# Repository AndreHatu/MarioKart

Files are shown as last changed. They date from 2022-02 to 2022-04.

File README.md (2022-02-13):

# Mario Kart with RC cars and ESP32s
This project aims at developing a real-life Mario Kart with RC cars and ESP32s.
The boards used utilize a single-core MCU (ESP-MINI-1 and ESP-SOLO-1). 
Schematics and wiring will be posted in the near future.

ECE477 Senior Design at Purdue University.

## How it works
We control RC cars with electronics replaced by our own ESP32. All communications are made using ESP-NOW, which is a Wi-Fi like wireless communication protocol. It enables low latency and long distance transmission of packets, with the only restriction they must be less than 250 bytes long.
Then, we place checkpoint towers and power-up blocks along the desired track and when cars run over them, a NFC tag is read and its information is sent to a central tower, which either updates records of checkpoints or determines what modifier to give the cars. Modifiers are randomly chosen using ESP's ```esp_random()``` function. Checkpoints are stored in two-dimensional arrays initialized upon race creation.

## Cloning
When cloning this repo, make sure to use ```git clone --recursive git@github.com:AndreHatu/MarioKart.git``` or run ```git submodule update --init --recursive``` after doing a standard clone. 
This ensures all dependencies are downloaded.

## Config, Build and Flash
To build, you will need to have installed Espressif's idf from their website.
Then run the following commands from a terminal.

```
idf.py set-target esp32
idf.py menuconfig
```
Inside the menuconfig, you might need to set the ```Components->freeRTOS->Run only on first core``` option in case your ESP32 only has one core (like the ones we are using for the project)
Then you can build and flash with
```
idf.py build
idf.py -p (PORT) flash
```

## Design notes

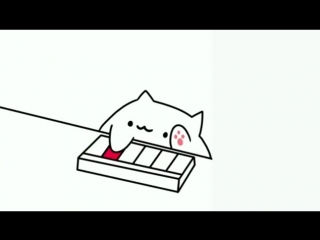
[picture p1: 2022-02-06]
spi_practice/main/image.jpg

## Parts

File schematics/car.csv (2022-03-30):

Source: | C:\Users\andre\prog\MarioKart\schematics\car.kicad_sch
Date: | 3/11/2022 11:44:14 AM
Tool: | Eeschema (6.0.2)
Generator: | C:\Program Files\KiCad\6.0\bin\scripting\plugins/bom_csv_grouped_by_value_with_fp.py
Component Count: | 44
Ref | Qnty | Value | Cmp name | Footprint | Description | Vendor
C1, | 1 | 22uF | C | Capacitor_SMD:C_0805_2012Metric | Unpolarized capacitor
C2, C4, C5, C6, | 4 | 100nF | C | Capacitor_SMD:C_0805_2012Metric | Unpolarized capacitor
C3, C7, | 2 | 100uF | C | Capacitor_THT:CP_Radial_D8.0mm_P5.00mm | Unpolarized capacitor
D1, D2, D3, D4, D5, D6, D7, D8, | 8 | IN4148 | DIODE | Diode_SMD:D_SOD-123F | Diode symbol for simulation only. Pin order incompatible with official kicad footprints
D9, | 1 | LED | LED | SamacSys_Parts:APHCM2012QBCDF01 | Light emitting diode
H1, H2, H3, H4, | 4 | MountingHole | MountingHole | MountingHole:MountingHole_2.5mm_Pad | Mounting Hole without connection
IC1, | 1 | ESP32-SOLO-1 | ESP32-SOLO-1 | RF_Module:ESP32-SOLO-ONE
J1, | 1 | Conn_01x09_Female | Conn_01x09_Female | Connector_PinHeader_2.54mm:PinHeader_1x09_P2.54mm_Vertical | Generic connector, single row, 01x09, script generated (kicad-library-utils/schlib/autogen/connector/)
J2, | 1 | Conn_01x04_Male | Conn_01x04_Male | Connector_PinHeader_2.54mm:PinHeader_1x04_P2.54mm_Vertical | Generic connector, single row, 01x04, script generated (kicad-library-utils/schlib/autogen/connector/)
J3, | 1 | Conn_01x02_Female | Conn_01x02_Female | Connector_PinHeader_2.54mm:PinHeader_1x02_P2.54mm_Vertical | Generic connector, single row, 01x02, script generated (kicad-library-utils/schlib/autogen/connector/)
J4, | 1 | Conn_01x06_Female | Conn_01x06_Female | Connector_PinHeader_2.54mm:PinHeader_1x06_P2.54mm_Vertical | Generic connector, single row, 01x06, script generated (kicad-library-utils/schlib/autogen/connector/)
J5, J6, | 2 | Conn_01x05_Female | Conn_01x05_Female | Connector_PinHeader_2.54mm:PinHeader_1x05_P2.54mm_Vertical | Generic connector, single row, 01x05, script generated (kicad-library-utils/schlib/autogen/connector/)
Q1, Q2, | 2 | SS8050-G | SS8050-G | SamacSys_Parts:SOT95P240X115-3N | Bipolar Transistors - BJT NPN TRANSISTOR 1.5A 40V
R1, R2, R3, R4, R5, R6, | 6 | 20 | R | Resistor_SMD:R_0805_2012Metric | Resistor
R7, R8, R9, R10, R11, R12, | 6 | 10k | R | Resistor_SMD:R_0805_2012Metric | Resistor
SW1, SW2, | 2 | SW_Push | SW_Push | Button_Switch_SMD:SW_SPST_CK_KXT3 | Push button switch, generic, two pins
U1, | 1 | L298HN | L298HN | Package_TO_SOT_THT:TO-220-15_P2.54x2.54mm_StaggerOdd_Lead4.58mm_Vertical | Dual full bridge motor driver, up to 46V, 4A, Multiwatt-15

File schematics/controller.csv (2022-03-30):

Source: | C:\Users\andre\prog\MarioKart\schematics\controller.kicad_sch
Date: | 3/11/2022 11:44:30 AM
Tool: | Eeschema (6.0.2)
Generator: | C:\Program Files\KiCad\6.0\bin\scripting\plugins/bom_csv_grouped_by_value.py
Component Count: | 33
Individual Components:
Item | Qty | Reference(s) | Value | LibPart | Footprint | Datasheet | Description | Height | Manufacturer_Name | Manufacturer_Part_Number | Mouser Part Number | Mouser Price/Stock
 |  | C1 | 0.1uF | Device:C | Capacitor_SMD:C_0805_2012Metric | ~
 |  | C2 | 0.1uF | Device:C | Capacitor_SMD:C_0805_2012Metric | ~
 |  | C3 | 100nF | Device:C | Capacitor_SMD:C_0805_2012Metric | ~
 |  | C4 | 22uF | Device:C | Capacitor_SMD:C_0805_2012Metric | ~
 |  | C5 | 100nF | Device:C | Capacitor_SMD:C_0805_2012Metric | ~
 |  | C6 | 10uF | Device:C | Capacitor_SMD:C_0805_2012Metric | ~
 |  | C7 | 10uF | Device:C | Capacitor_SMD:C_0805_2012Metric | ~
 |  | D1 | LED | Device:LED | Mouser:APHCM2012QBCDF01 | ~
 |  | IC1 | AZ1117CD-3.3TRG1 | Mouser:AZ1117CD-3.3TRG1 | Mouser:AZ1117CD33TRG1 | https://www.diodes.com/assets/Datasheets/AZ1117C.pdf | LDO Regulator Pos 3.3V 0.8A 3-Pin(2+Tab) TO-252 T/R | 2.38 | Diodes Inc. | AZ1117CD-3.3TRG1 | 621-AZ1117CD-3.3TRG1 | https://www.mouser.co.uk/ProductDetail/Diodes-Incorporated/AZ1117CD-33TRG1?qs=FKu9oBikfSnei3n4%2FTBoVg%3D%3D
 |  | IC2 | ESP32-SOLO-1 | ESP-SOLO-1:ESP32-SOLO-1 | RF_Module:ESP32-WROOM-32 | https://www.espressif.com/sites/default/files/documentation/esp32-solo-1_datasheet_en.pdf | WiFi Modules (802.11) SMD Module, ESP32-S0WD, 32Mbits SPI flash, UART mode, |  | Espressif Systems | ESP32-SOLO-1 | 356-ESP32-SOLO-1 | https://www.mouser.co.uk/ProductDetail/Espressif-Systems/ESP32-SOLO-1?qs=w%2Fv1CP2dgqpIFRWX9FvikA%3D%3D
 |  | J1 | Conn_01x05 | Connector_Generic:Conn_01x05 | Connector_PinSocket_2.54mm:PinSocket_1x05_P2.54mm_Vertical | ~
 |  | J2 | Conn_01x05 | Connector_Generic:Conn_01x05 | Connector_PinSocket_2.54mm:PinSocket_1x05_P2.54mm_Vertical | ~
 |  | J3 | Conn_01x06 | Connector_Generic:Conn_01x06 | Connector_PinSocket_2.54mm:PinSocket_1x06_P2.54mm_Vertical | ~
 |  | Q1 | SS8050-G | Mouser:SS8050-G | Mouser:SOT95P240X115-3N | https://datasheet.datasheetarchive.com/originals/distributors/DKDS-12/229454.pdf | Bipolar Transistors - BJT NPN TRANSISTOR 1.5A 40V | 1.15 | Comchip Technology | SS8050-G | 750-SS8050-G | https://www.mouser.co.uk/ProductDetail/Comchip-Technology/SS8050-G?qs=LLUE9lz1YbcHg%252BWLMAtcrQ%3D%3D
 |  | Q2 | SS8050-G | Mouser:SS8050-G | Mouser:SOT95P240X115-3N | https://datasheet.datasheetarchive.com/originals/distributors/DKDS-12/229454.pdf | Bipolar Transistors - BJT NPN TRANSISTOR 1.5A 40V | 1.15 | Comchip Technology | SS8050-G | 750-SS8050-G | https://www.mouser.co.uk/ProductDetail/Comchip-Technology/SS8050-G?qs=LLUE9lz1YbcHg%252BWLMAtcrQ%3D%3D
 |  | R1 | 10k | Device:R | Resistor_SMD:R_0805_2012Metric | ~
 |  | R2 | 10k | Device:R | Resistor_SMD:R_0805_2012Metric | ~
 |  | R3 | 10k | Device:R | Resistor_SMD:R_0805_2012Metric | ~
 |  | R4 | 10k | Device:R | Resistor_SMD:R_0805_2012Metric | ~
 |  | R5 | 10k | Device:R | Resistor_SMD:R_0805_2012Metric | ~
 |  | R6 | 10k | Device:R | Resistor_SMD:R_0805_2012Metric | ~
 |  | R7 | 10k | Device:R | Resistor_SMD:R_0805_2012Metric | ~
 |  | R8 | 10k | Device:R | Resistor_SMD:R_0805_2012Metric | ~
 |  | R9 | 0 | Device:R | Resistor_SMD:R_0805_2012Metric | ~
 |  | R10 | 10k | Device:R | Resistor_SMD:R_0805_2012Metric | ~
 |  | R11 | 10k | Device:R | Resistor_SMD:R_0805_2012Metric | ~
 |  | SW1 | SW_Push | Switch:SW_Push | Button_Switch_SMD:SW_SPST_CK_KXT3 | ~
 |  | SW2 | SW_Push | Switch:SW_Push | Button_Switch_SMD:SW_SPST_CK_KXT3 | ~
 |  | SW3 | SW_Push_Dual | Switch:SW_Push_Dual | Button_Switch_THT:SW_TH_Tactile_Omron_B3F-10xx | ~
 |  | SW4 | SW_Push_Dual | Switch:SW_Push_Dual | Button_Switch_THT:SW_TH_Tactile_Omron_B3F-10xx | ~
 |  | SW5 | SW_Push_Dual | Switch:SW_Push_Dual | Button_Switch_THT:SW_TH_Tactile_Omron_B3F-10xx | ~
 |  | SW6 | SW_Push_Dual | Switch:SW_Push_Dual | Button_Switch_THT:SW_TH_Tactile_Omron_B3F-10xx | ~
 |  | SW7 | SW_Push_Dual | Switch:SW_Push_Dual | Button_Switch_THT:SW_TH_Tactile_Omron_B3F-10xx | ~
Collated Components:
Item | Qty | Reference(s) | Value | LibPart | Footprint | Datasheet | Description | Height | Manufacturer_Name | Manufacturer_Part_Number | Mouser Part Number | Mouser Price/Stock
1 | 2 | C1, C2 | 0.1uF | Device:C | Capacitor_SMD:C_0805_2012Metric | ~
2 | 2 | C3, C5 | 100nF | Device:C | Capacitor_SMD:C_0805_2012Metric | ~
3 | 1 | C4 | 22uF | Device:C | Capacitor_SMD:C_0805_2012Metric | ~
4 | 2 | C6, C7 | 10uF | Device:C | Capacitor_SMD:C_0805_2012Metric | ~
5 | 1 | D1 | LED | Device:LED | Mouser:APHCM2012QBCDF01 | ~
6 | 1 | IC1 | AZ1117CD-3.3TRG1 | Mouser:AZ1117CD-3.3TRG1 | Mouser:AZ1117CD33TRG1 | https://www.diodes.com/assets/Datasheets/AZ1117C.pdf | LDO Regulator Pos 3.3V 0.8A 3-Pin(2+Tab) TO-252 T/R | 2.38 | Diodes Inc. | AZ1117CD-3.3TRG1 | 621-AZ1117CD-3.3TRG1 | https://www.mouser.co.uk/ProductDetail/Diodes-Incorporated/AZ1117CD-33TRG1?qs=FKu9oBikfSnei3n4%2FTBoVg%3D%3D
7 | 1 | IC2 | ESP32-SOLO-1 | ESP-SOLO-1:ESP32-SOLO-1 | RF_Module:ESP32-WROOM-32 | https://www.espressif.com/sites/default/files/documentation/esp32-solo-1_datasheet_en.pdf | WiFi Modules (802.11) SMD Module, ESP32-S0WD, 32Mbits SPI flash, UART mode, |  | Espressif Systems | ESP32-SOLO-1 | 356-ESP32-SOLO-1 | https://www.mouser.co.uk/ProductDetail/Espressif-Systems/ESP32-SOLO-1?qs=w%2Fv1CP2dgqpIFRWX9FvikA%3D%3D
8 | 2 | J1, J2 | Conn_01x05 | Connector_Generic:Conn_01x05 | Connector_PinSocket_2.54mm:PinSocket_1x05_P2.54mm_Vertical | ~
9 | 1 | J3 | Conn_01x06 | Connector_Generic:Conn_01x06 | Connector_PinSocket_2.54mm:PinSocket_1x06_P2.54mm_Vertical | ~
10 | 2 | Q1, Q2 | SS8050-G | Mouser:SS8050-G | Mouser:SOT95P240X115-3N | https://datasheet.datasheetarchive.com/originals/distributors/DKDS-12/229454.pdf | Bipolar Transistors - BJT NPN TRANSISTOR 1.5A 40V | 1.15 | Comchip Technology | SS8050-G | 750-SS8050-G | https://www.mouser.co.uk/ProductDetail/Comchip-Technology/SS8050-G?qs=LLUE9lz1YbcHg%252BWLMAtcrQ%3D%3D
11 | 10 | R1, R2, R3, R4, R5, R6, R7, R8, R10, R11 | 10k | Device:R | Resistor_SMD:R_0805_2012Metric | ~
12 | 1 | R9 | 0 | Device:R | Resistor_SMD:R_0805_2012Metric | ~
13 | 2 | SW1, SW2 | SW_Push | Switch:SW_Push | Button_Switch_SMD:SW_SPST_CK_KXT3 | ~
14 | 5 | SW3, SW4, SW5, SW6, SW7 | SW_Push_Dual | Switch:SW_Push_Dual | Button_Switch_THT:SW_TH_Tactile_Omron_B3F-10xx | ~

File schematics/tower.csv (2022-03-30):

Source: | C:\Users\andre\prog\MarioKart\schematics\tower.kicad_sch
Date: | 3/11/2022 11:44:42 AM
Tool: | Eeschema (6.0.2)
Generator: | C:\Program Files\KiCad\6.0\bin\scripting\plugins/bom_csv_grouped_by_value.py
Component Count: | 27
Individual Components:
Item | Qty | Reference(s) | Value | LibPart | Footprint | Datasheet | Description | Height | Manufacturer_Name | Manufacturer_Part_Number | Mouser Part Number | Mouser Price/Stock
 |  | C1 | 0.1uF | Device:C | Capacitor_SMD:C_0805_2012Metric | ~
 |  | C2 | 0.1uF | Device:C | Capacitor_SMD:C_0805_2012Metric | ~
 |  | C3 | 100nF | Device:C | Capacitor_SMD:C_0805_2012Metric | ~
 |  | C4 | 22uF | Device:C | Capacitor_SMD:C_0805_2012Metric | ~
 |  | C5 | 100nF | Device:C | Capacitor_SMD:C_0805_2012Metric | ~
 |  | C6 | 100nF | Device:C | Capacitor_SMD:C_0805_2012Metric | ~
 |  | C7 | 100nF | Device:C | Capacitor_SMD:C_0805_2012Metric | ~
 |  | D1 | BAT760-7 | Mouser:BAT760-7 | Mouser:SOD2513X120N | https://www.diodes.com/assets/Datasheets/ds30498.pdf | Diode Schottky 30V 1A 2Pin SOD323 Diodes Inc BAT760-7, SMT Schottky Diode, 30V 1A, 2-Pin SOD-323 | 1.2 | Diodes Inc. | BAT760-7 | 621-BAT760-7 | https://www.mouser.co.uk/ProductDetail/Diodes-Incorporated/BAT760-7?qs=JV7lzlMm3yKDDyO09xoRbQ%3D%3D
 |  | D2 | LED | Device:LED | Mouser:APHCM2012QBCDF01 | ~
 |  | IC1 | ESP32-SOLO-1 | tower-rescue:ESP32-SOLO-1-ESP-SOLO-1-controller-rescue | RF_Module:ESP32-WROOM-32 | https://www.espressif.com/sites/default/files/documentation/esp32-solo-1_datasheet_en.pdf | WiFi Modules (802.11) SMD Module, ESP32-S0WD, 32Mbits SPI flash, UART mode, |  | Espressif Systems | ESP32-SOLO-1 | 356-ESP32-SOLO-1 | https://www.mouser.co.uk/ProductDetail/Espressif-Systems/ESP32-SOLO-1?qs=w%2Fv1CP2dgqpIFRWX9FvikA%3D%3D
 |  | J1 | USB_B_Micro | Connector:USB_B_Micro | Connector_USB:USB_Micro-B_Molex-105017-0001 | ~
 |  | J2 | Conn_01x06 | Connector_Generic:Conn_01x06 | Connector_PinSocket_2.54mm:PinSocket_1x06_P2.54mm_Vertical | ~
 |  | J3 | Conn_01x05 | Connector_Generic:Conn_01x05 | Connector_PinSocket_2.54mm:PinSocket_1x05_P2.54mm_Vertical | ~
 |  | J4 | SD_Card | Connector:SD_Card | Connector_Card:SD_Kyocera_145638109211859+ | http://portal.fciconnect.com/Comergent//fci/drawing/10067847.pdf
 |  | J5 | Conn_02x10_Odd_Even | Connector_Generic:Conn_02x10_Odd_Even | Connector_PinSocket_2.54mm:PinSocket_2x10_P2.54mm_Vertical | ~
 |  | Q1 | SS8050-G | Mouser:SS8050-G | Mouser:SOT95P240X115-3N | https://datasheet.datasheetarchive.com/originals/distributors/DKDS-12/229454.pdf | Bipolar Transistors - BJT NPN TRANSISTOR 1.5A 40V | 1.15 | Comchip Technology | SS8050-G | 750-SS8050-G | https://www.mouser.co.uk/ProductDetail/Comchip-Technology/SS8050-G?qs=LLUE9lz1YbcHg%252BWLMAtcrQ%3D%3D
 |  | Q2 | SS8050-G | Mouser:SS8050-G | Mouser:SOT95P240X115-3N | https://datasheet.datasheetarchive.com/originals/distributors/DKDS-12/229454.pdf | Bipolar Transistors - BJT NPN TRANSISTOR 1.5A 40V | 1.15 | Comchip Technology | SS8050-G | 750-SS8050-G | https://www.mouser.co.uk/ProductDetail/Comchip-Technology/SS8050-G?qs=LLUE9lz1YbcHg%252BWLMAtcrQ%3D%3D
 |  | R1 | 10k | Device:R | Resistor_SMD:R_0805_2012Metric | ~
 |  | R2 | 10k | Device:R | Resistor_SMD:R_0805_2012Metric | ~
 |  | R3 | 10k | Device:R | Resistor_SMD:R_0805_2012Metric | ~
 |  | R4 | 10k | Device:R | Resistor_SMD:R_0805_2012Metric | ~
 |  | R5 | 10k | Device:R | Resistor_SMD:R_0805_2012Metric | ~
 |  | R6 | 0 | Device:R | Resistor_SMD:R_0805_2012Metric | ~
 |  | R7 | 0 | Device:R | Resistor_SMD:R_0805_2012Metric | ~
 |  | R8 | 10k | Device:R | Resistor_SMD:R_0805_2012Metric | ~
 |  | SW1 | SW_Push | Switch:SW_Push | Button_Switch_SMD:SW_SPST_CK_KXT3 | ~
 |  | SW2 | SW_Push | Switch:SW_Push | Button_Switch_SMD:SW_SPST_CK_KXT3 | ~
Collated Components:
Item | Qty | Reference(s) | Value | LibPart | Footprint | Datasheet | Description | Height | Manufacturer_Name | Manufacturer_Part_Number | Mouser Part Number | Mouser Price/Stock
1 | 2 | C1, C2 | 0.1uF | Device:C | Capacitor_SMD:C_0805_2012Metric | ~
2 | 4 | C3, C5, C6, C7 | 100nF | Device:C | Capacitor_SMD:C_0805_2012Metric | ~
3 | 1 | C4 | 22uF | Device:C | Capacitor_SMD:C_0805_2012Metric | ~
4 | 1 | D1 | BAT760-7 | Mouser:BAT760-7 | Mouser:SOD2513X120N | https://www.diodes.com/assets/Datasheets/ds30498.pdf | Diode Schottky 30V 1A 2Pin SOD323 Diodes Inc BAT760-7, SMT Schottky Diode, 30V 1A, 2-Pin SOD-323 | 1.2 | Diodes Inc. | BAT760-7 | 621-BAT760-7 | https://www.mouser.co.uk/ProductDetail/Diodes-Incorporated/BAT760-7?qs=JV7lzlMm3yKDDyO09xoRbQ%3D%3D
5 | 1 | D2 | LED | Device:LED | Mouser:APHCM2012QBCDF01 | ~
6 | 1 | IC1 | ESP32-SOLO-1 | tower-rescue:ESP32-SOLO-1-ESP-SOLO-1-controller-rescue | RF_Module:ESP32-WROOM-32 | https://www.espressif.com/sites/default/files/documentation/esp32-solo-1_datasheet_en.pdf | WiFi Modules (802.11) SMD Module, ESP32-S0WD, 32Mbits SPI flash, UART mode, |  | Espressif Systems | ESP32-SOLO-1 | 356-ESP32-SOLO-1 | https://www.mouser.co.uk/ProductDetail/Espressif-Systems/ESP32-SOLO-1?qs=w%2Fv1CP2dgqpIFRWX9FvikA%3D%3D
7 | 1 | J1 | USB_B_Micro | Connector:USB_B_Micro | Connector_USB:USB_Micro-B_Molex-105017-0001 | ~
8 | 1 | J2 | Conn_01x06 | Connector_Generic:Conn_01x06 | Connector_PinSocket_2.54mm:PinSocket_1x06_P2.54mm_Vertical | ~
9 | 1 | J3 | Conn_01x05 | Connector_Generic:Conn_01x05 | Connector_PinSocket_2.54mm:PinSocket_1x05_P2.54mm_Vertical | ~
10 | 1 | J4 | SD_Card | Connector:SD_Card | Connector_Card:SD_Kyocera_145638109211859+ | http://portal.fciconnect.com/Comergent//fci/drawing/10067847.pdf
11 | 1 | J5 | Conn_02x10_Odd_Even | Connector_Generic:Conn_02x10_Odd_Even | Connector_PinSocket_2.54mm:PinSocket_2x10_P2.54mm_Vertical | ~
12 | 2 | Q1, Q2 | SS8050-G | Mouser:SS8050-G | Mouser:SOT95P240X115-3N | https://datasheet.datasheetarchive.com/originals/distributors/DKDS-12/229454.pdf | Bipolar Transistors - BJT NPN TRANSISTOR 1.5A 40V | 1.15 | Comchip Technology | SS8050-G | 750-SS8050-G | https://www.mouser.co.uk/ProductDetail/Comchip-Technology/SS8050-G?qs=LLUE9lz1YbcHg%252BWLMAtcrQ%3D%3D
13 | 6 | R1, R2, R3, R4, R5, R8 | 10k | Device:R | Resistor_SMD:R_0805_2012Metric | ~
14 | 2 | R6, R7 | 0 | Device:R | Resistor_SMD:R_0805_2012Metric | ~
15 | 2 | SW1, SW2 | SW_Push | Switch:SW_Push | Button_Switch_SMD:SW_SPST_CK_KXT3 | ~

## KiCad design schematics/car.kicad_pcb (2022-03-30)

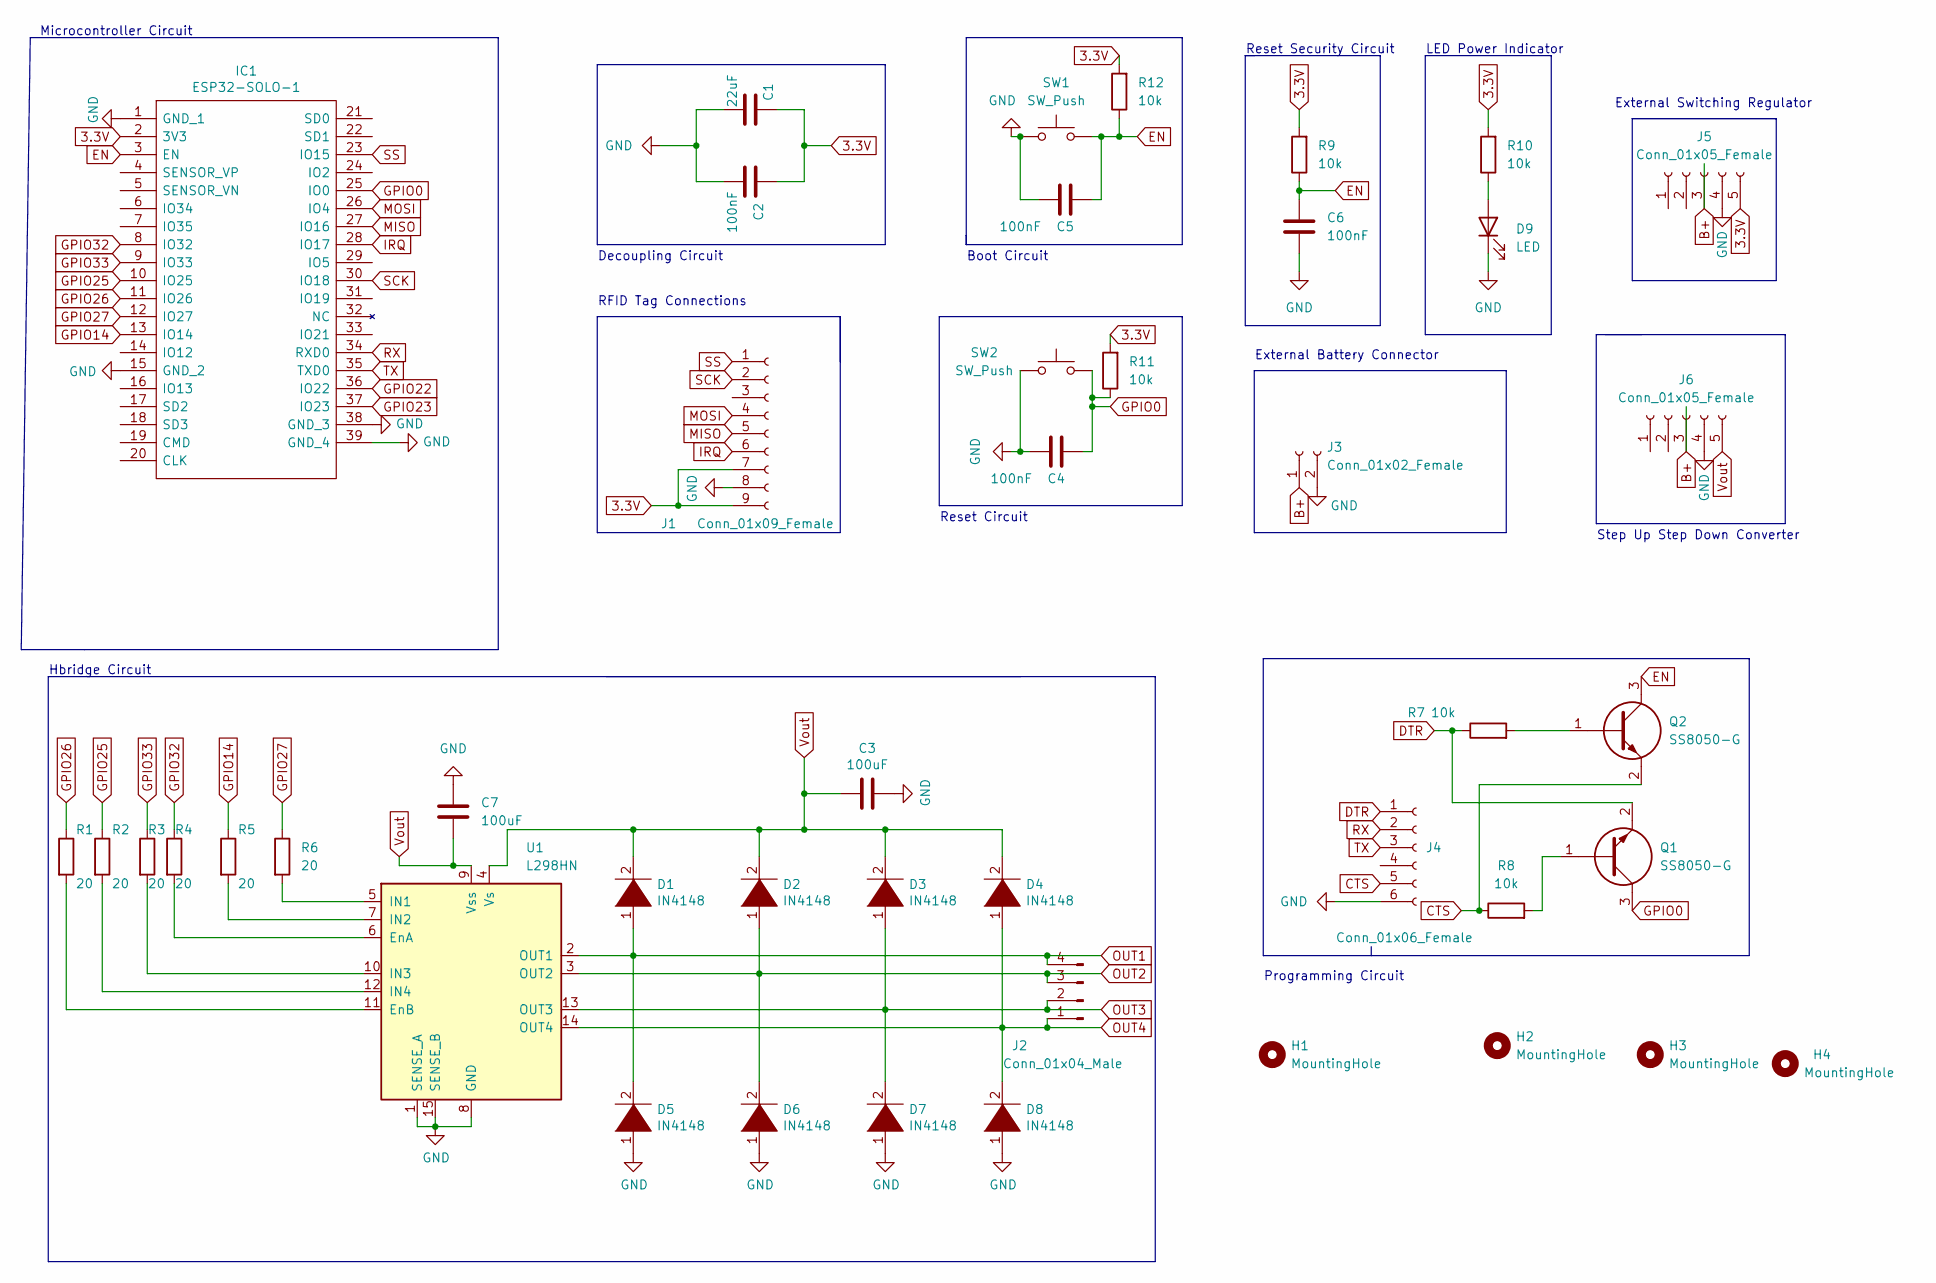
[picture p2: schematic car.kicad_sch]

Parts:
C1: 22uF; C_0805_2012Metric
C2, C4, C5, C6: 100nF; C_0805_2012Metric
C3, C7: 100uF; CP_Radial_D8.0mm_P5.00mm
D1, D2, D3, D4, D5, D6, D7, D8: IN4148; D_SOD-123F
D9: LED; APHCM2012QBCDF01
H1, H2, H3, H4: MountingHole; MountingHole_2.5mm_Pad
IC1: ESP32-SOLO-1; ESP32-SOLO-ONE; Manufacturer_Part_Number ESP32-SOLO-1; Mouser Part Number 356-ESP32-SOLO-1
J1: Conn_01x09_Female; PinHeader_1x09_P2.54mm_Vertical
J2: Conn_01x04_Male; PinHeader_1x04_P2.54mm_Vertical
J3: Conn_01x02_Female; PinHeader_1x02_P2.54mm_Vertical
J4: Conn_01x06_Female; PinHeader_1x06_P2.54mm_Vertical
J5, J6: Conn_01x05_Female; PinHeader_1x05_P2.54mm_Vertical
Q1, Q2: SS8050-G; SOT95P240X115-3N; Mouser Part Number 750-SS8050-G
R1, R2, R3, R4, R5, R6: 20; R_0805_2012Metric
R7, R8, R9, R10, R11, R12: 10k; R_0805_2012Metric
SW1, SW2: SW_Push; SW_SPST_CK_KXT3
U1: L298HN; TO-220-15_P2.54x2.54mm_StaggerOdd_Lead4.58mm_Vertical

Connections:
3.3V: C1.1, C2.1, IC1.2 (3V3), J1.7, J1.9, J5.5, R9.2, R10.2, R11.2, R12.2
B+: J3.1, J5.3, J6.3
CTS: J4.5, Q2.2, R8.1
DTR: J4.1, Q1.2, R7.1
EN: C5.2, C6.1, IC1.3 (EN), Q2.3, R9.1, R12.1, SW1.2
GND: C1.2, C2.2, C3.1, C4.1, C5.1, C6.2, C7.1, D5.1 (K), D6.1 (K), D7.1 (K), D8.1 (K), D9.1 (K), IC1.1 (GND_1), IC1.15 (GND_2), IC1.38 (GND_3), IC1.39 (GND_4), J1.8, J3.2, J4.6, J5.4, J6.4, SW1.1, SW2.1, U1.1 (SENSE_A), U1.8 (GND), U1.15 (SENSE_B)
GPIO0: C4.2, IC1.25 (IO0), Q1.3, R11.1, SW2.2
GPIO14: IC1.13 (IO14), R5.1
GPIO22: IC1.36 (IO22)
GPIO23: IC1.37 (IO23)
GPIO25: IC1.10 (IO25), R2.1
GPIO26: IC1.11 (IO26), R1.1
GPIO27: IC1.12 (IO27), R6.1
GPIO32: IC1.8 (IO32), R4.1
GPIO33: IC1.9 (IO33), R3.1
IRQ: IC1.28 (IO17), J1.6
MISO: IC1.27 (IO16), J1.5
MOSI: IC1.26 (IO4), J1.4
unnamed: D9.2 (A), R10.1
unnamed: Q1.1, R8.2
unnamed: Q2.1, R7.2
unnamed: R1.2, U1.11 (EnB)
unnamed: R2.2, U1.12 (IN4)
unnamed: R3.2, U1.10 (IN3)
unnamed: R4.2, U1.6 (EnA)
unnamed: R5.2, U1.7 (IN2)
unnamed: R6.2, U1.5 (IN1)
OUT1: D1.1 (K), D5.2 (A), J2.4, U1.2 (OUT1)
OUT2: D2.1 (K), D6.2 (A), J2.3, U1.3 (OUT2)
OUT3: D3.1 (K), D7.2 (A), J2.2, U1.13 (OUT3)
OUT4: D4.1 (K), D8.2 (A), J2.1, U1.14 (OUT4)
RX: IC1.34 (RXD0), J4.2
SCK: IC1.30 (IO18), J1.2
SS: IC1.23 (IO15), J1.1
TX: IC1.35 (TXD0), J4.3
Vout: C3.2, C7.2, D1.2 (A), D2.2 (A), D3.2 (A), D4.2 (A), J6.5, U1.4 (Vs), U1.9 (Vss)

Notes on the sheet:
Step Up Step Down Converter
Boot Circuit
Microcontroller Circuit
Programming Circuit
External Switching Regulator
External Battery Connector
Hbridge Circuit
Decoupling Circuit
RFID Tag Connections
Reset Circuit
Reset Security Circuit
LED Power Indicator

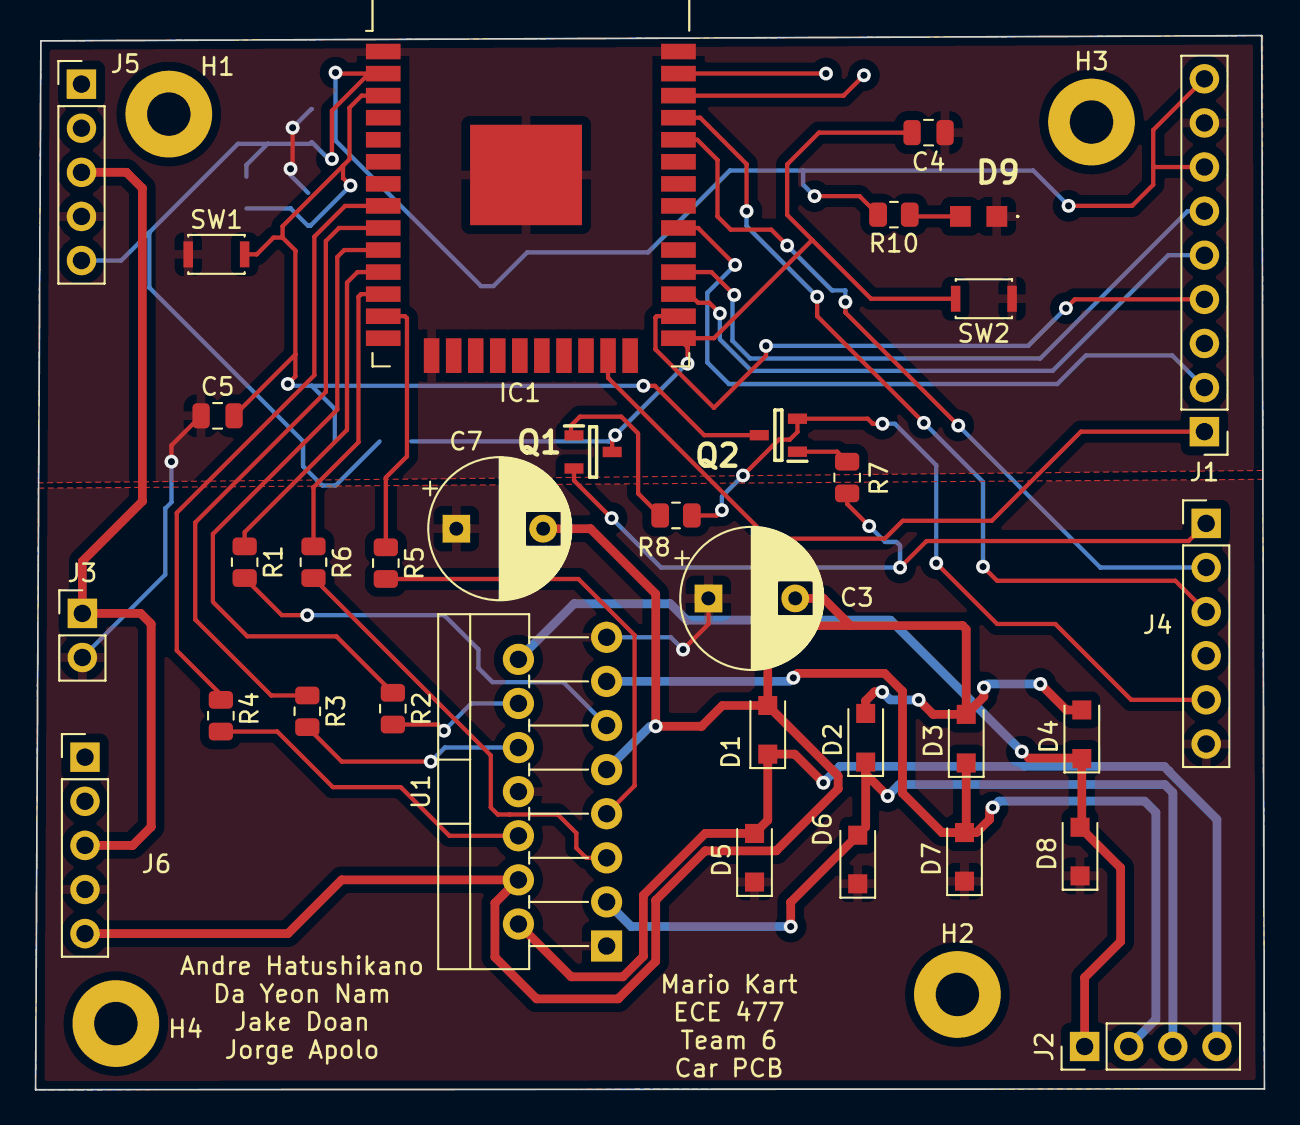
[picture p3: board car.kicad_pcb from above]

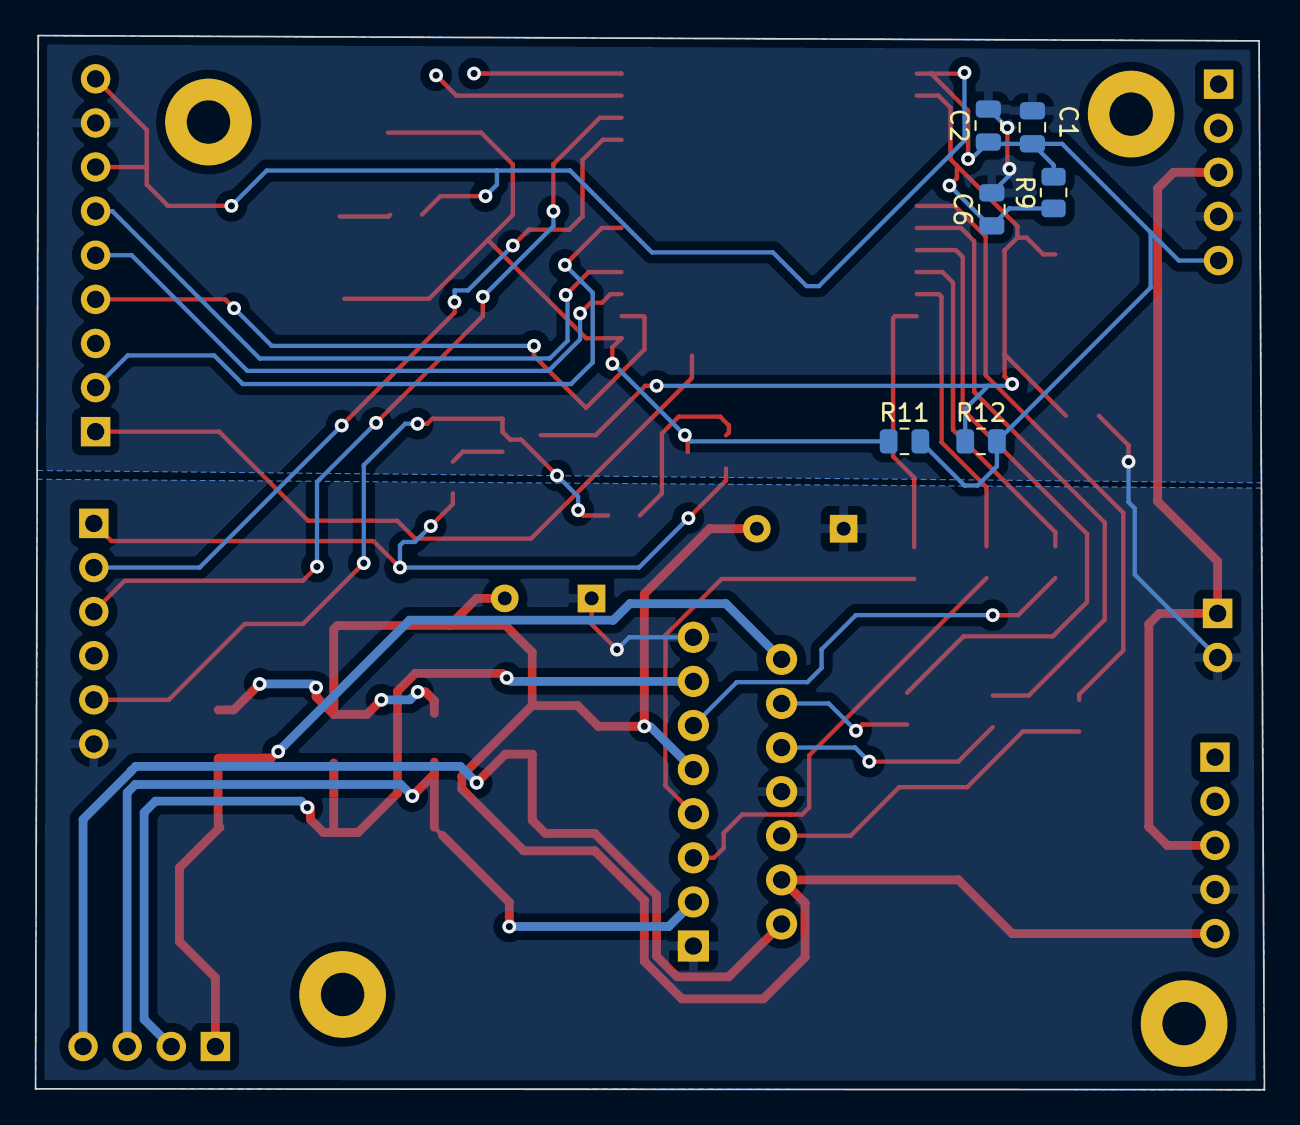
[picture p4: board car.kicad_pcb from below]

Board: 2 copper layers, 70.8 x 60.7 mm, 44 parts (6 on the bottom side), 34 nets.

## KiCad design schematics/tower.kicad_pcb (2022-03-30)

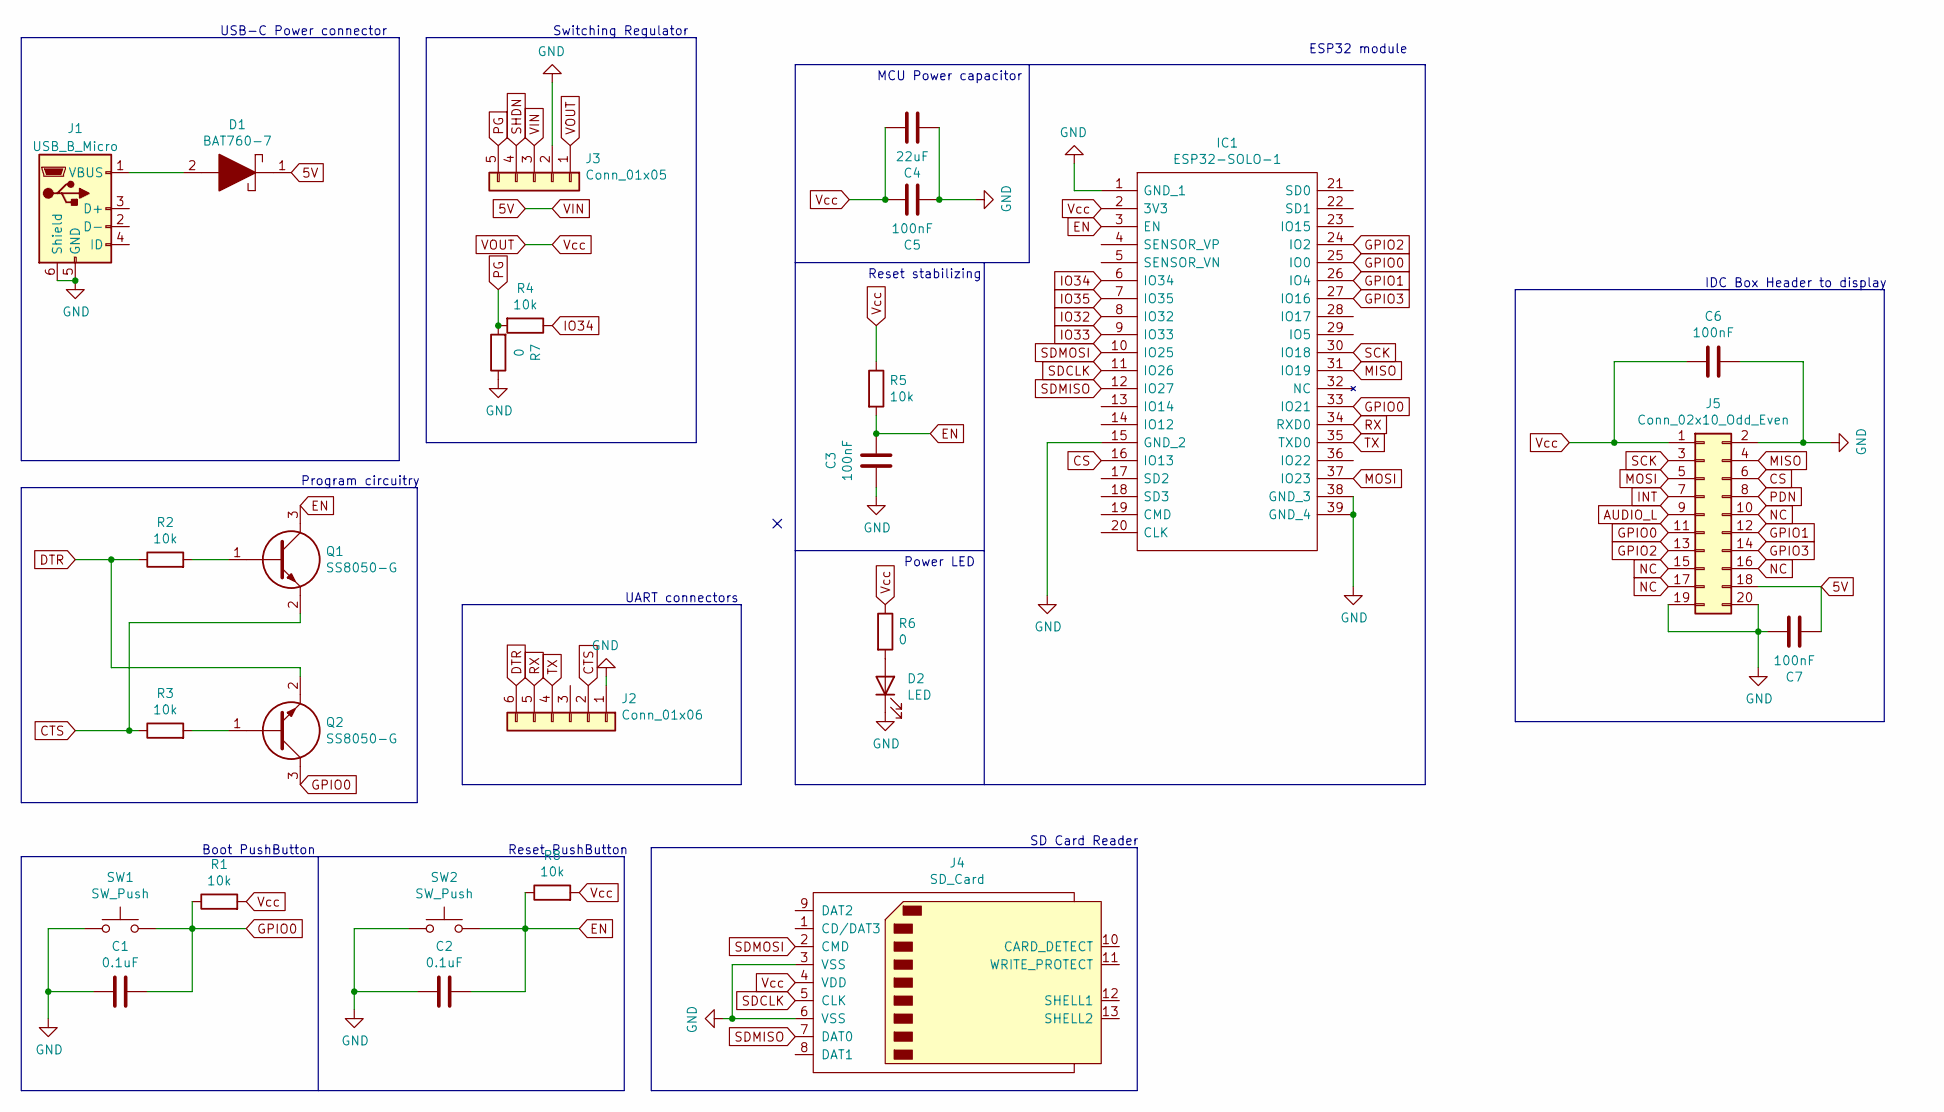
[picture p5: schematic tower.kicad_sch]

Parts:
C1, C2: 0.1uF; C_0805_2012Metric
C3, C5, C6, C7: 100nF; C_0805_2012Metric
C4: 22uF; C_0805_2012Metric
D1: BAT760-7; SOD2513X120N; Mouser Part Number 621-BAT760-7
D2: LED; APHCM2012QBCDF01
IC1: ESP32-SOLO-1; ESP32-WROOM-32; Manufacturer_Part_Number ESP32-SOLO-1; Mouser Part Number 356-ESP32-SOLO-1
J1: USB_B_Micro; USB_Micro-B_Molex-105017-0001
J2: Conn_01x06; PinSocket_1x06_P2.54mm_Vertical
J3: Conn_01x05; PinSocket_1x05_P2.54mm_Vertical
J4: SD_Card; SD_Kyocera_145638109211859+
J5: Conn_02x10_Odd_Even; PinSocket_2x10_P2.54mm_Vertical
Q1, Q2: SS8050-G; SOT95P240X115-3N; Mouser Part Number 750-SS8050-G
R1, R2, R3, R4, R5, R8: 10k; R_0805_2012Metric
R6, R7: 0; R_0805_2012Metric
SW1, SW2: SW_Push; SW_SPST_CK_KXT3

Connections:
5V: C7.2, D1.1, J3.3, J5.18
AUDIO_L: J5.9
CS: IC1.16 (IO13), J5.6
CTS: J2.2, Q1.2, R3.1
DTR: J2.6, Q2.2, R2.1
EN: C2.1, C3.1, IC1.3 (EN), Q1.3, R5.2, R8.1, SW2.2
GND: C1.2, C2.2, C3.2, C4.2, C5.2, C6.1, C7.1, D2.1 (K), IC1.1 (GND_1), IC1.15 (GND_2), IC1.38 (GND_3), IC1.39 (GND_4), J1.5 (GND), J1.6 (Shield), J2.1, J3.2, J4.3 (VSS), J4.6 (VSS), J5.2, J5.19, J5.20, R7.1, SW1.1, SW2.1
GPIO0: C1.1, IC1.25 (IO0), IC1.33 (IO21), J5.11, Q2.3, R1.1, SW1.2
GPIO1: IC1.26 (IO4), J5.12
GPIO2: IC1.24 (IO2), J5.13
GPIO3: IC1.27 (IO16), J5.14
INT: J5.7
IO32: IC1.8 (IO32)
IO33: IC1.9 (IO33)
IO34: IC1.6 (IO34), R4.1
IO35: IC1.7 (IO35)
MISO: IC1.31 (IO19), J5.4
MOSI: IC1.37 (IO23), J5.5
NC: J5.10, J5.15, J5.16, J5.17
unnamed: D2.2 (A), R6.2
unnamed: D1.2, J1.1 (VBUS)
unnamed: Q1.1, R2.2
unnamed: Q2.1, R3.2
PDN: J5.8
PG: J3.5, R4.2, R7.2
RX: IC1.34 (RXD0), J2.5
SCK: IC1.30 (IO18), J5.3
SDCLK: IC1.11 (IO26), J4.5 (CLK)
SDMISO: IC1.12 (IO27), J4.7 (DAT0)
SDMOSI: IC1.10 (IO25), J4.2 (CMD)
SHDN: J3.4
TX: IC1.35 (TXD0), J2.4
VOUT: C4.1, C5.1, C6.2, IC1.2 (3V3), J3.1, J4.4 (VDD), J5.1, R1.2, R5.1, R6.1, R8.2

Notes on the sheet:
Program circuitry
ESP32 module
IDC Box Header to display
Reset PushButton
Switching Regulator
SD Card Reader
Reset stabilizing
USB-C Power connector
UART connectors
Power LED
MCU Power capacitor
Boot PushButton

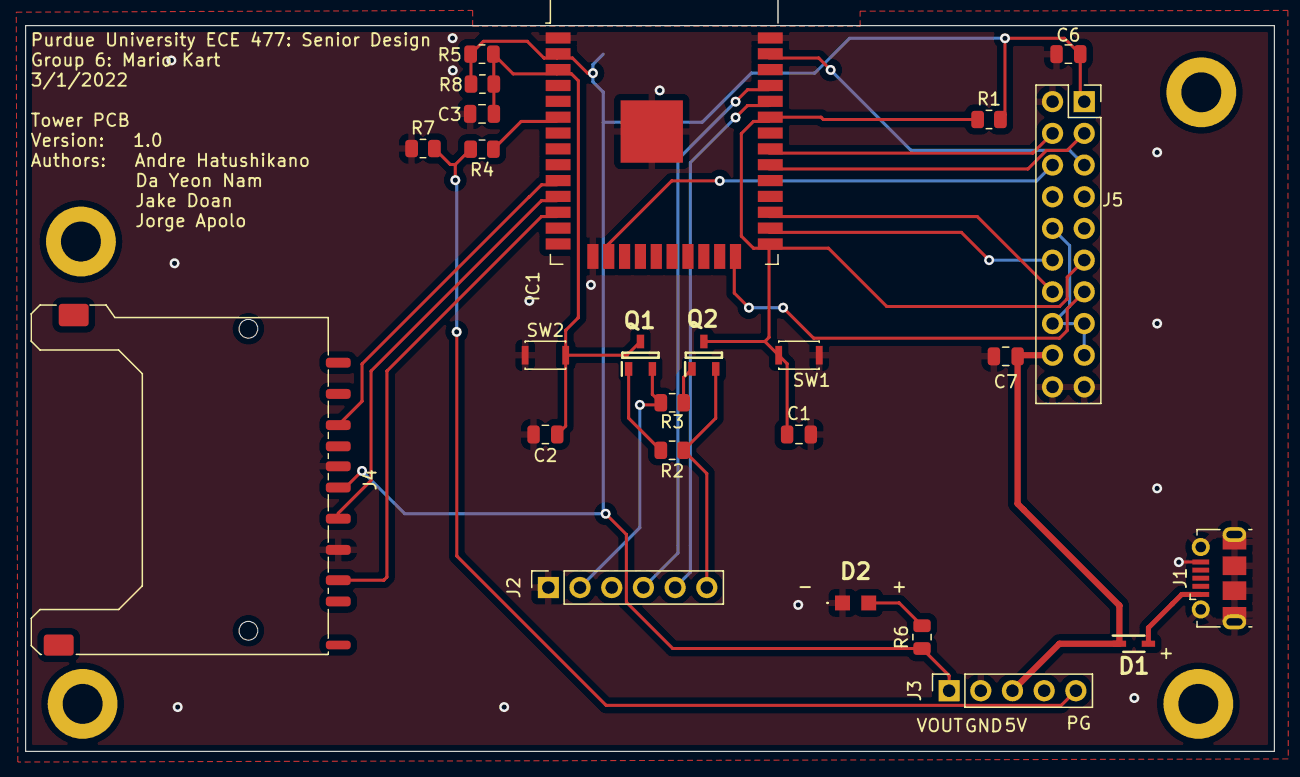
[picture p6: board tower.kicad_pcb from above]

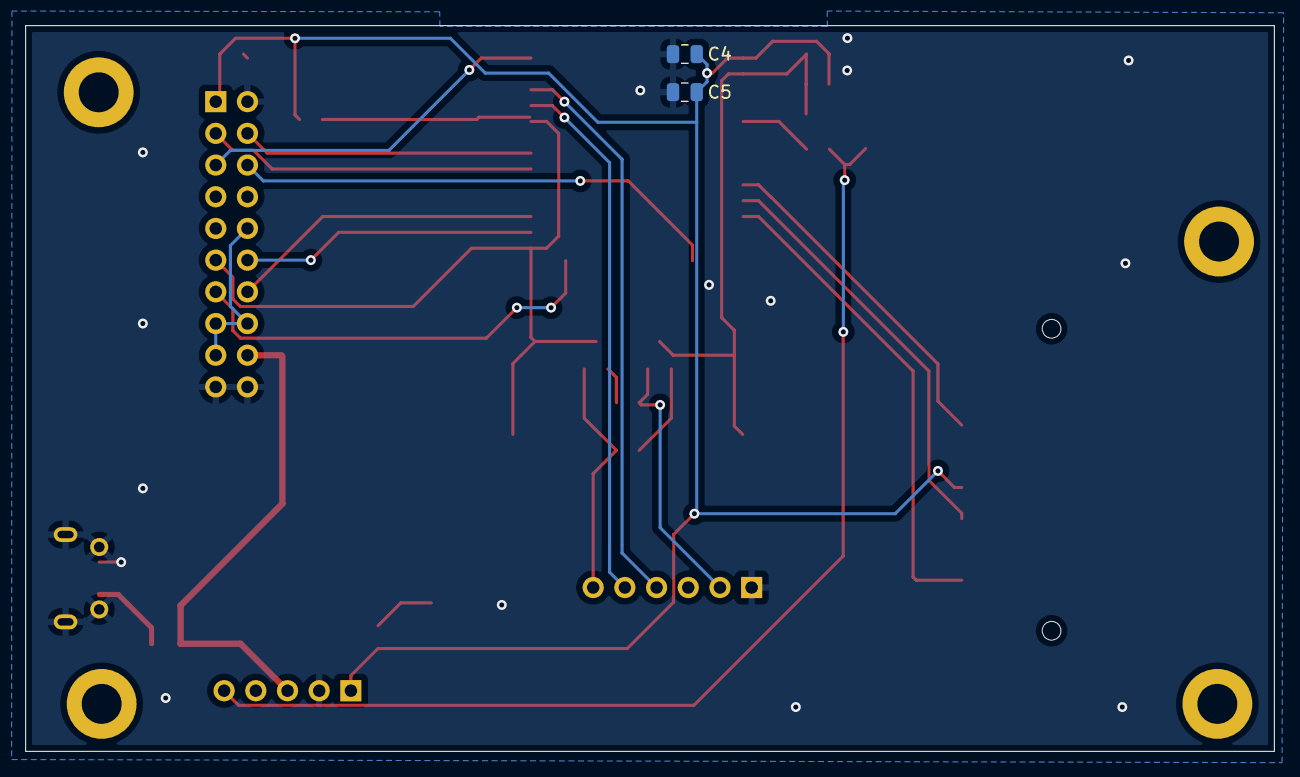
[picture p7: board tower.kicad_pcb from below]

Board: 2 copper layers, 100.1 x 58.2 mm, 27 parts (2 on the bottom side), 26 nets.

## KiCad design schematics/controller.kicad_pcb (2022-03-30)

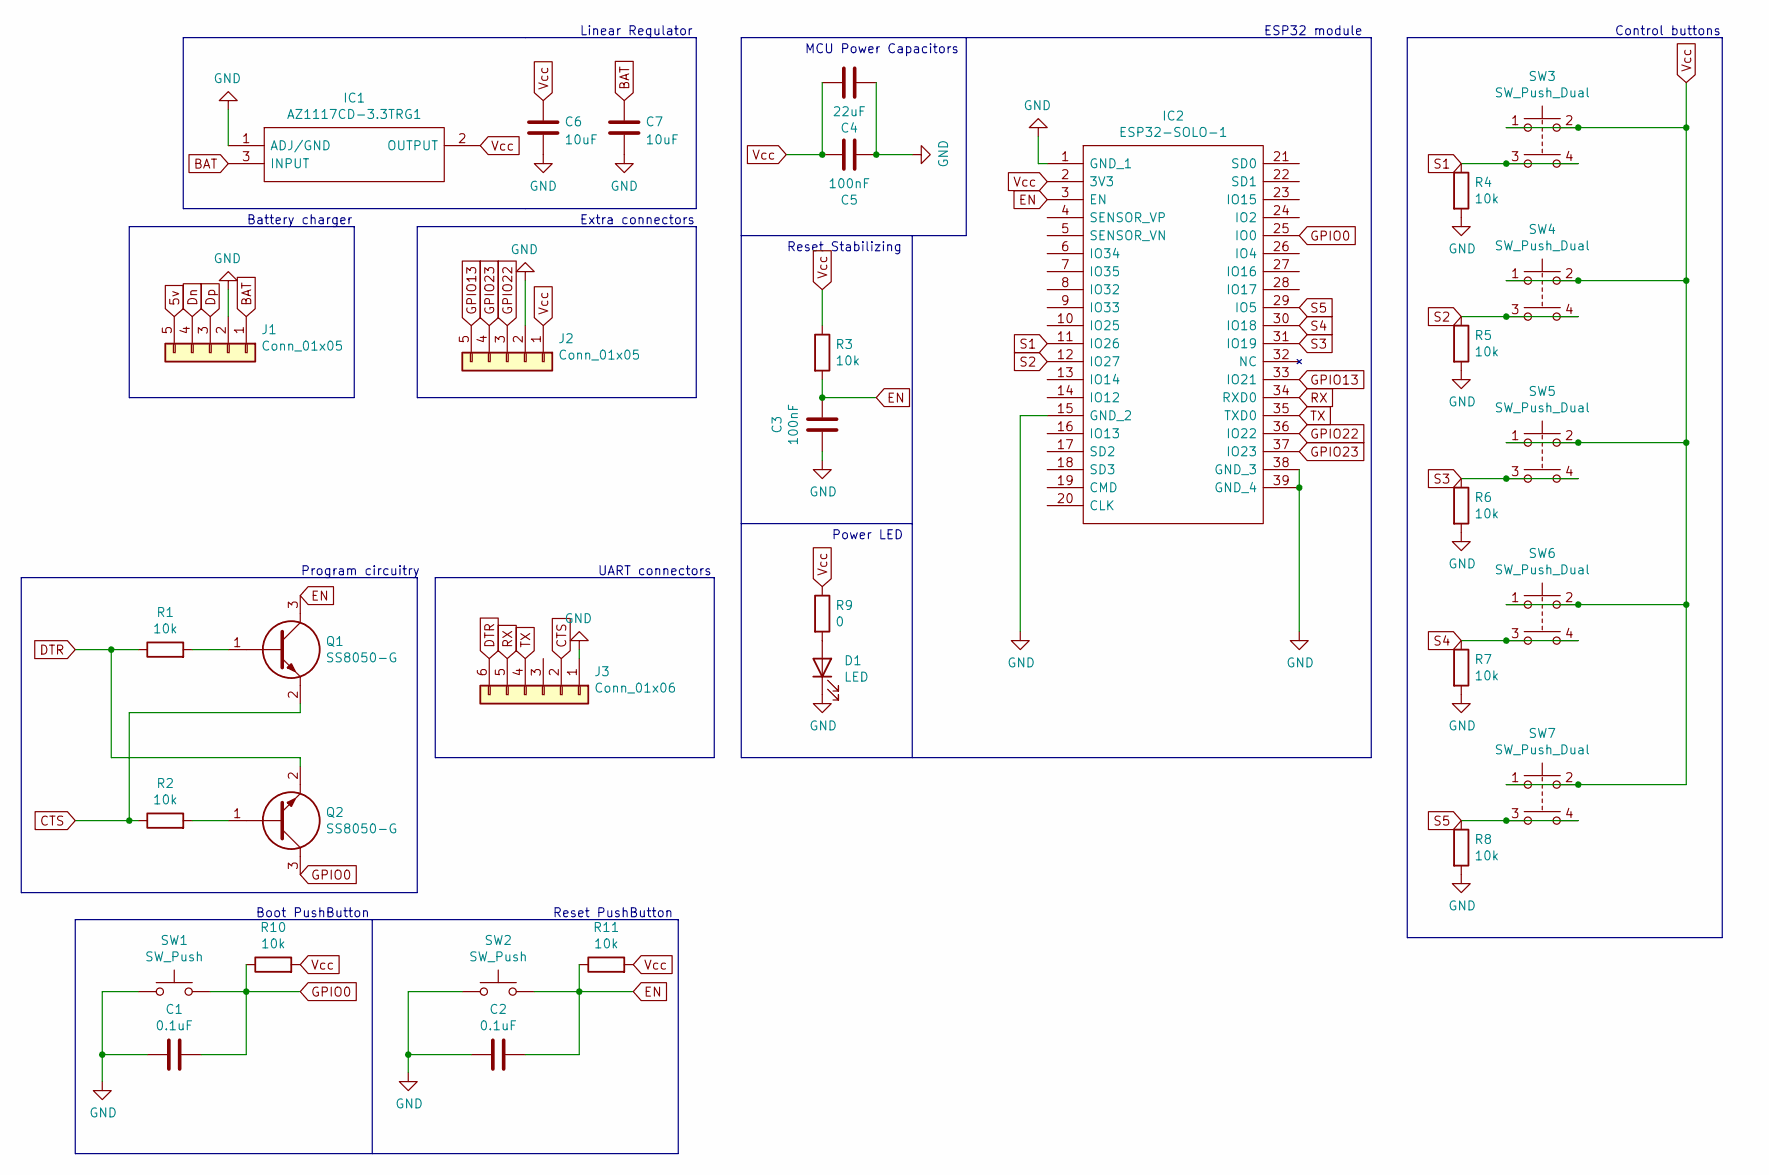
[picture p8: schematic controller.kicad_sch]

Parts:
C1, C2: 0.1uF; C_0805_2012Metric
C3, C5: 100nF; C_0805_2012Metric
C4: 22uF; C_0805_2012Metric
C6, C7: 10uF; C_0805_2012Metric
D1: LED; APHCM2012QBCDF01
IC1: AZ1117CD-3.3TRG1; AZ1117CD33TRG1; Mouser Part Number 621-AZ1117CD-3.3TRG1
IC2: ESP32-SOLO-1; ESP32-WROOM-32; Manufacturer_Part_Number ESP32-SOLO-1; Mouser Part Number 356-ESP32-SOLO-1
J1, J2: Conn_01x05; PinSocket_1x05_P2.54mm_Vertical
J3: Conn_01x06; PinSocket_1x06_P2.54mm_Vertical
Q1, Q2: SS8050-G; SOT95P240X115-3N; Mouser Part Number 750-SS8050-G
R1, R2, R3, R4, R5, R6, R7, R8, R10, R11: 10k; R_0805_2012Metric
R9: 0; R_0805_2012Metric
SW1, SW2: SW_Push; SW_SPST_CK_KXT3
SW3, SW4, SW5, SW6, SW7: SW_Push_Dual; SW_TH_Tactile_Omron_B3F-10xx

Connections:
5v: J1.5
BAT: C7.1, IC1.3 (INPUT), J1.1
CTS: J3.2, Q1.2, R2.1
DTR: J3.6, Q2.2, R1.1
Dn: J1.4
Dp: J1.3
EN: C2.1, C3.1, IC2.3 (EN), Q1.3, R3.2, R11.1, SW2.2
GND: C1.2, C2.2, C3.2, C4.2, C5.2, C6.2, C7.2, D1.1 (K), IC1.1 (ADJ/GND), IC2.1 (GND_1), IC2.15 (GND_2), IC2.38 (GND_3), IC2.39 (GND_4), J1.2, J2.2, J3.1, R4.2, R5.2, R6.2, R7.2, R8.2, SW1.1, SW2.1
GPIO0: C1.1, IC2.25 (IO0), Q2.3, R10.1, SW1.2
GPIO13: IC2.33 (IO21), J2.5
GPIO22: IC2.36 (IO22), J2.3
GPIO23: IC2.37 (IO23), J2.4
unnamed: D1.2 (A), R9.2
unnamed: Q1.1, R1.2
unnamed: Q2.1, R2.2
RX: IC2.34 (RXD0), J3.5
S1: IC2.11 (IO26), R4.1, SW3.3, SW3.4
S2: IC2.12 (IO27), R5.1, SW4.3, SW4.4
S3: IC2.31 (IO19), R6.1, SW5.3, SW5.4
S4: IC2.30 (IO18), R7.1, SW6.3, SW6.4
S5: IC2.29 (IO5), R8.1, SW7.3, SW7.4
TX: IC2.35 (TXD0), J3.4
Vcc: C4.1, C5.1, C6.1, IC1.2 (OUTPUT), IC2.2 (3V3), J2.1, R3.1, R9.1, R10.2, R11.2, SW3.1, SW3.2, SW4.1, SW4.2, SW5.1, SW5.2, SW6.1, SW6.2, SW7.1, SW7.2

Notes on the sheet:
Boot PushButton
MCU Power Capacitors
Control buttons
Linear Regulator
Extra connectors
UART connectors
Program circuitry
Reset Stabilizing
Power LED
ESP32 module
Reset PushButton
Battery charger

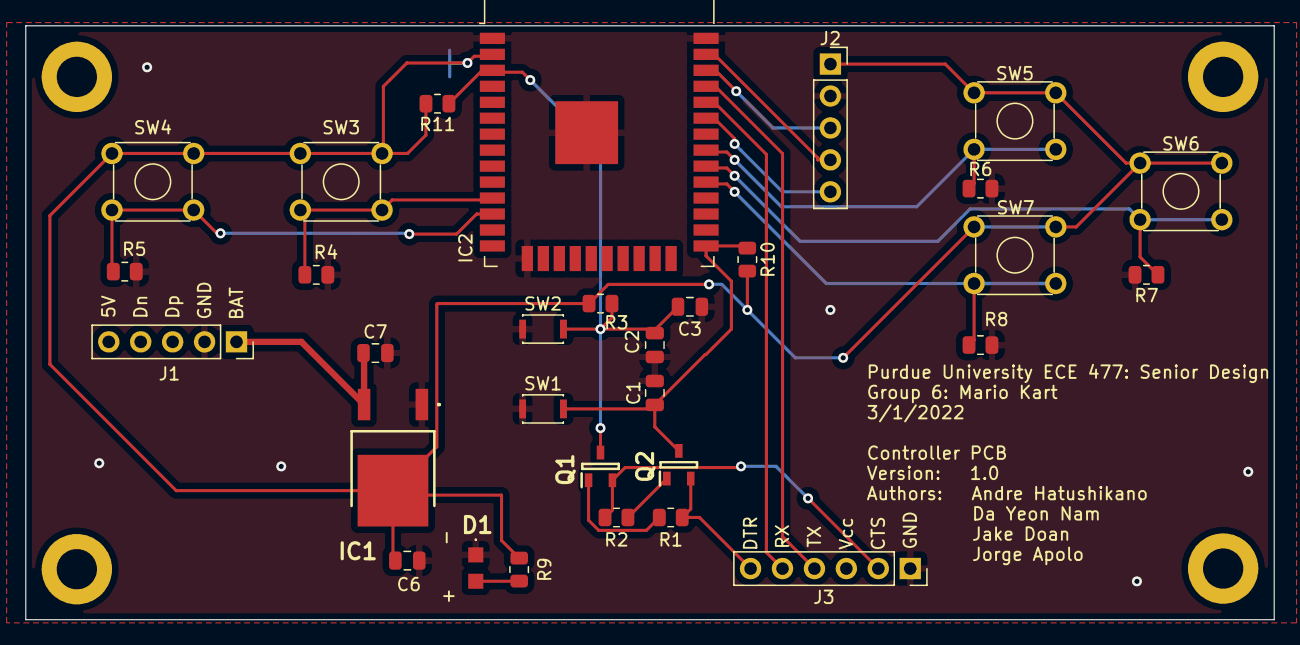
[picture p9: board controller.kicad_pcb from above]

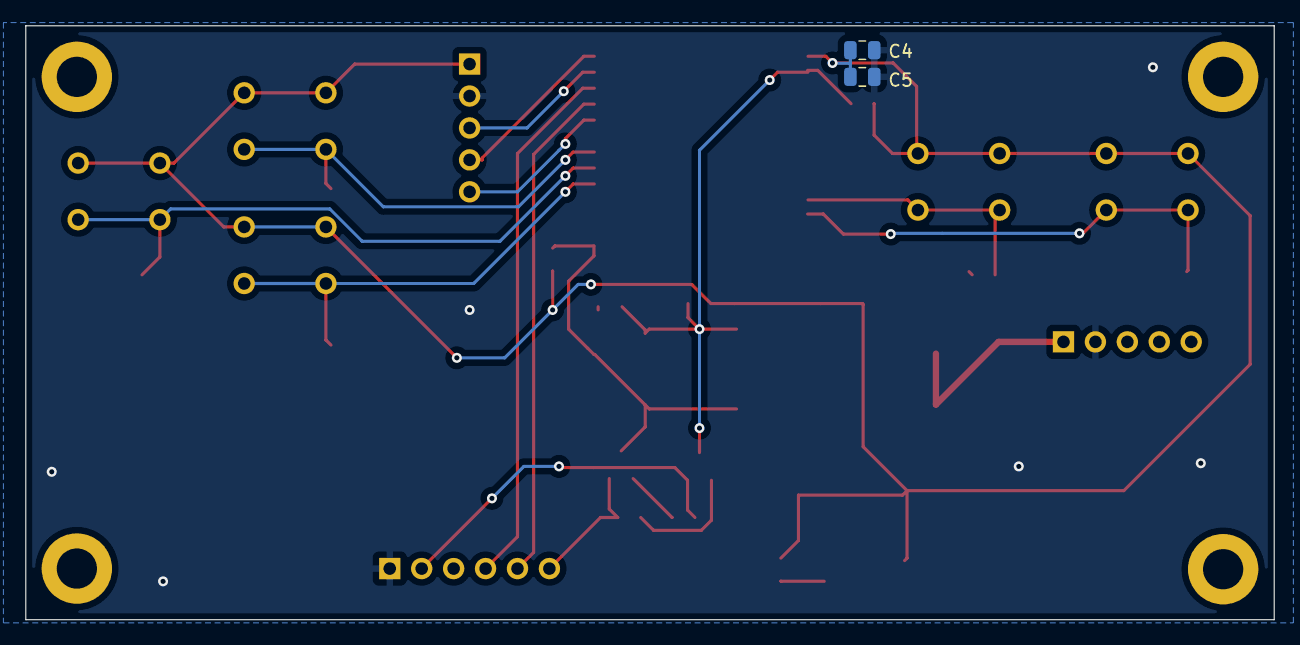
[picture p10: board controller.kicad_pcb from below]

Board: 2 copper layers, 99.3 x 47.2 mm, 33 parts (2 on the bottom side), 20 nets.

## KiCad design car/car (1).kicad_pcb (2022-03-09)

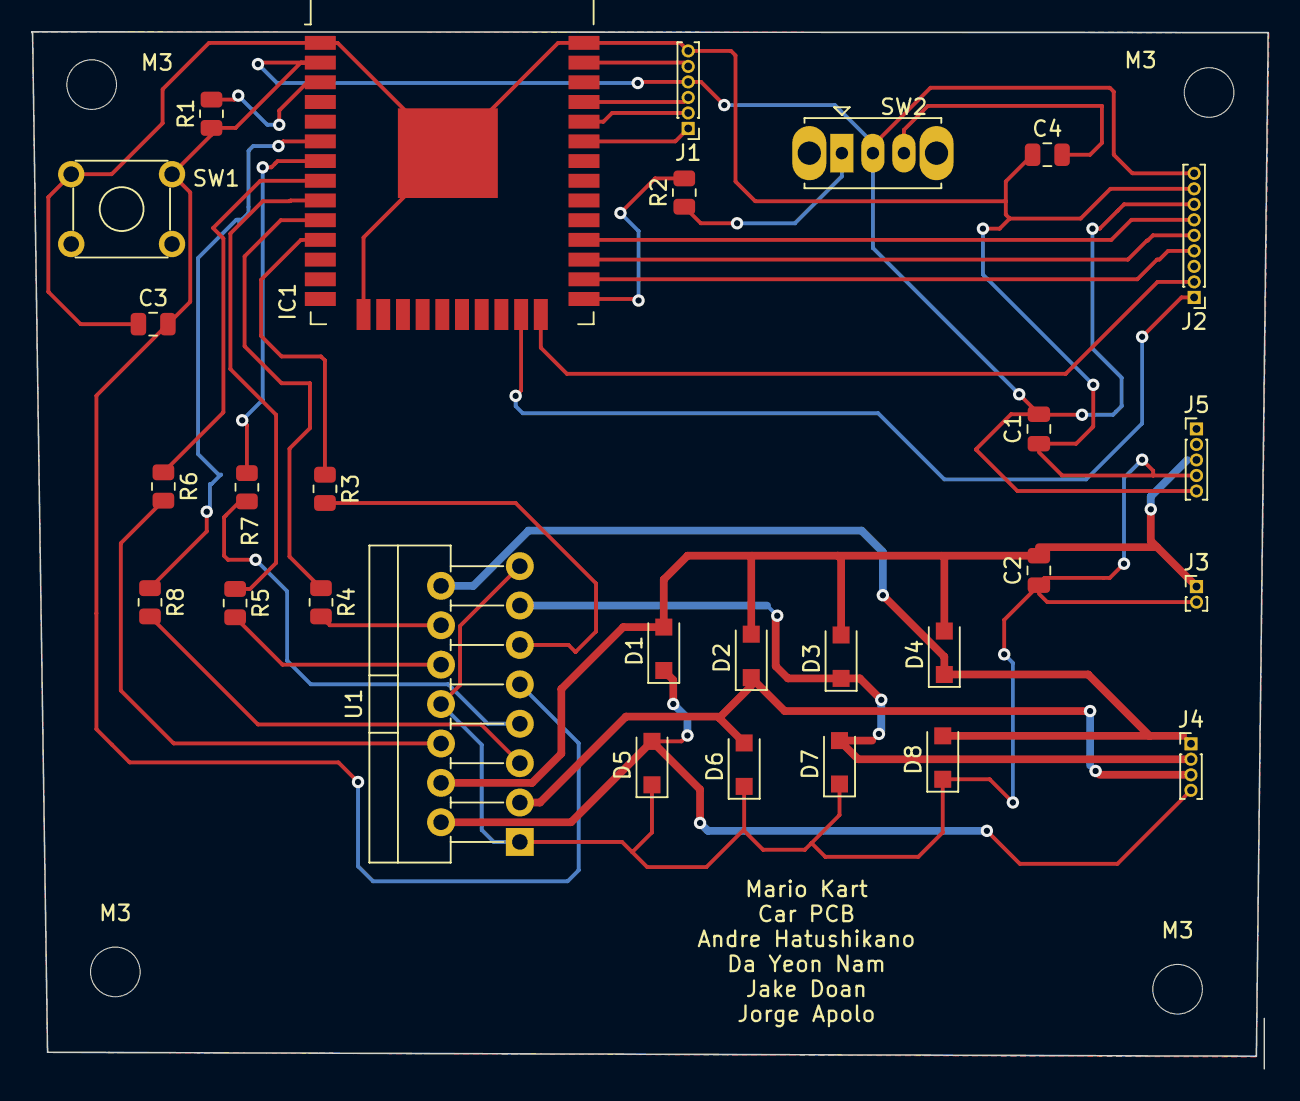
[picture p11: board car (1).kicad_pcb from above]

Board: 2 copper layers, 79.7 x 66.9 mm, 33 parts (0 on the bottom side), 24 nets.

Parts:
C1, C2: 100nF; C_0805_2012Metric
C3, C4: 100uF; C_0805_2012Metric
D1, D2, D3, D4, D5, D6, D7, D8: IN4148; D_SOD-123F
IC1: ESP32-SOLO-1; ESP32-SOLO-ONE
J1: Conn_01x06_Female; PinHeader_1x06_P1.00mm_Vertical
J2: Conn_01x09_Female; PinHeader_1x09_P1.00mm_Vertical
J3: Conn_01x02_Female; PinHeader_1x02_P1.00mm_Vertical
J4: Conn_01x04_Male; PinHeader_1x04_P1.00mm_Vertical
J5: Conn_01x05_Female; PinHeader_1x05_P1.00mm_Vertical
M3, M3#2, M3#3, M3#4: MountingHole_3.2mm_M3_DIN965
R1, R2: 10k; R_0805_2012Metric
R3, R4, R5, R6, R7, R8: 20; R_0805_2012Metric
SW1: SW_Push; SW_TH_Tactile_Omron_B3F-10xx
SW2: SW_SPDT; SW_Slide_1P2T_CK_OS102011MS2Q
U1: L298HN; TO-220-15_P2.54x2.54mm_StaggerOdd_Lead4.58mm_Vertical

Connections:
+3V3: C1.2, C3.2, IC1.2 (3V3), J1.4, J2.7, J2.9, J5.5, R1.1, SW1.2, SW2.2 (B), U1.9 (Vss)
+9V: C2.2, D1.2 (A), D2.2 (A), D3.2 (A), D4.2 (A), J3.1, J5.3, U1.4 (Vs)
GND: C1.1, C2.1, C3.1, C4.1, D5.1 (K), D6.1 (K), D7.1 (K), D8.1 (K), IC1.1 (GND_1), IC1.15 (GND_2), IC1.38 (GND_3), IC1.39 (GND_4), J1.6, J2.8, J3.2, J5.4, SW1.1, U1.1 (SENSE_A), U1.8 (GND), U1.15 (SENSE_B)
unnamed: C4.2, SW2.3 (C)
unnamed: IC1.3 (EN), R1.2
unnamed: IC1.8 (IO32), R6.1
unnamed: IC1.9 (IO33), R5.1
unnamed: IC1.10 (IO25), R4.1
unnamed: IC1.11 (IO26), R3.1
unnamed: IC1.12 (IO27), R8.1
unnamed: IC1.13 (IO14), R7.1
unnamed: IC1.23 (IO15), J2.1
unnamed: IC1.24 (IO2), J2.2
unnamed: IC1.25 (IO0), R2.2
unnamed: IC1.26 (IO4), J2.4
unnamed: IC1.27 (IO16), J2.5
unnamed: IC1.28 (IO17), J2.6
unnamed: IC1.34 (RXD0), J1.2
unnamed: IC1.35 (TXD0), J1.3
unnamed: R2.1, SW2.1 (A)
OUT1: D1.1 (K), D5.2 (A), J4.4, U1.2 (OUT1)
OUT2: D2.1 (K), D6.2 (A), J4.3, U1.3 (OUT2)
OUT3: D3.1 (K), D7.2 (A), J4.2, U1.13 (OUT3)
OUT4: D4.1 (K), D8.2 (A), J4.1, U1.14 (OUT4)

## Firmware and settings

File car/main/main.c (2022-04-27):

#include "rc522.h"
#include <stdio.h>
#include <string.h>
#include <stdlib.h>
#include <stdbool.h>
#include <sys/time.h>
#include "freertos/FreeRTOS.h"
#include "freertos/task.h"
#include "freertos/event_groups.h"
#include "freertos/queue.h"
#include "driver/gpio.h"
#include "nvs_flash.h"
#include "esp_netif.h"
#include "esp_wifi.h"
#include "esp_log.h"
#include "esp_now.h"
#include "esp_system.h"
#include "esp_sleep.h"

#include "../../config/mario_kart_config.h"

#include "driver/mcpwm.h"
#include "soc/mcpwm_periph.h"
#include "esp_attr.h"
#include "soc/rtc.h"
#include "pwm.h"

// NOTE: change accordingly
#define TOWER TOWER_MAC_ADDR
#define CONTROLLER CONTROLLER1_MAC_ADDR
#define ANOTHER_CAR	CAR2_MAC_ADDR
#define MY_CAR CAR1_MAC_ADDR
#define MOTOR_PIN_BW 14   // in3
#define MOTOR_PIN_FW 27   // in4
#define MOTOR_PIN_LEFT 33  // in2
#define MOTOR_PIN_RIGHT 25 // in1
//#define MOD 15 // in1

static xQueueHandle ctrl_recv_q;
static xQueueHandle tag_q;
static xQueueHandle tower_recv_q;
static xQueueHandle mod_q;
static xQueueHandle active_mod_q;
static bool mod_flag;
static bool rev;

int start_time;
int current_time;

int64_t millis() {
	struct timeval tv;
	gettimeofday(&tv, NULL);
	return (tv.tv_sec * 1000LL + (tv.tv_usec / 1000LL));
}

void print_packet(controls_packet packet, bool rev){
	// printf(packet.left ? "left |" : "     |");
	// printf(packet.right ? "right |" : "      |");
	// printf(packet.up ? "up |" : "   |");
	// printf(packet.down ? "down \n" : "     \n");
	// printf(packet.mod ? "mod \n" : "     \n");
	if (!rev){
		gpio_set_level(MOTOR_PIN_FW, packet.up);
		gpio_set_level(MOTOR_PIN_BW, packet.down);
		gpio_set_level(MOTOR_PIN_LEFT, packet.left);
		gpio_set_level(MOTOR_PIN_RIGHT, packet.right);
	}
	else{	
		gpio_set_level(MOTOR_PIN_FW, packet.down);
		gpio_set_level(MOTOR_PIN_BW, packet.up);
		gpio_set_level(MOTOR_PIN_LEFT, packet.right);
		gpio_set_level(MOTOR_PIN_RIGHT, packet.left);
	}	
}


static void tag_queue_send_task(void *p) // sending rfid tag info to central tower
{
	tag_packet packet;// = malloc(sizeof(tag_packet));
	const uint8_t DEST_MAC[] = TOWER; // TOWER_MAC_ADDR, changed for testing
	esp_err_t err;
	while(1)
	{
		ESP_LOGI("Car", "Trying to send packet to tower");
		if (xQueueReceive(tag_q, &packet, portMAX_DELAY) == pdTRUE){
			ESP_LOGI("Car", "Sending packet to tower");
			if((err = esp_now_send(DEST_MAC, (uint8_t*)&packet, sizeof(tag_packet))) != ESP_OK){
				ESP_LOGE("Car", "Error sending packet to tower");
				printf("Error: %x\n", err);
			}
		}
		else{
			taskYIELD();
		}
	}
}

// receive controls process
static void ctrl_queue_process_task(void *p)
{
    controls_packet recv_packet;
	rev = 0;
    ESP_LOGI("Car", "Listening_to_controls");
    for(;;){
		// ESP_LOGI("Car", "Trying to process controls packet");
        if(xQueueReceive(ctrl_recv_q, &recv_packet, portMAX_DELAY) == pdTRUE) {
			print_packet(recv_packet,rev);
			if (mod_flag){
				current_time = millis();
				if (current_time - start_time >= 3000){
					printf("Back to normal state\n");
					//printf("start time %d current time %d", start_time, current_time);
					brushed_motor_a(MCPWM_UNIT_0, MCPWM_TIMER_0, V0);
					mod_flag = 0;
					rev = 0;
				}
			}

			// User click modifier button
			else if (recv_packet.mod == true){
				printf("mod = 1\n");
				modifier_packet mod_pack;// = malloc(sizeof(modifier_packet));
				used_mod_packet used_mod;
				esp_err_t err;

				if (xQueueReceive(mod_q, &mod_pack, 0) == pdTRUE){
					printf("have something in mod queue\n");
					used_mod.modifier = mod_pack.modifier;
					const uint8_t TOWER_MAC[MAC_LEN] = TOWER_MAC_ADDR;
					if((err = esp_now_send(TOWER_MAC, (uint8_t*)&used_mod, sizeof(used_mod_packet))) != ESP_OK){
						ESP_LOGE("Car", "Error sending packet to tower");
						printf("Error: %x\n", err);
					}
					if (mod_pack.modifier == 0){
						start_time = millis()-1500;
						//current_time = start_time;
						printf("modifier: power up\n");
						brushed_motor_a(MCPWM_UNIT_0, MCPWM_TIMER_0, VSPEED);
						mod_flag = 1;
					}
					else 
					{
						//printf("modifier: something else\n");

						active_mod_packet act_pack;// = malloc(sizeof(active_mod_packet));
						act_pack.modifier = mod_pack.modifier;
						const uint8_t DEST_MAC[MAC_LEN] = ANOTHER_CAR;
						if((err = esp_now_send(DEST_MAC, (uint8_t*)&act_pack, sizeof(active_mod_packet))) != ESP_OK){
							ESP_LOGE("Car", "Error sending packet to tower");
							printf("Error: %x\n", err);
						}
						start_time = millis();
						mod_flag = 1;
					}
				}
				else{
					ESP_LOGI("car", "No Modifier Available");
				}
			}
        }        
    }
}

// receive modifiers process
static void tower_queue_process_task(void *p)
{
    modifier_packet recv_packet;
    ESP_LOGI("Car", "Listening_to_modifiers");
    for(;;)
    {
		ESP_LOGI("Car", "Trying to process modifier packet");
        if(xQueueReceive(tower_recv_q, &recv_packet, portMAX_DELAY) == pdTRUE)
        {
            // print_packet(recv_packet);
			printf("Received modifier: %02x\n", recv_packet.modifier);
			xQueueSend(mod_q, &recv_packet, 0);
        }  
		else{
			taskYIELD();
		}   

    }
}

//activate the modifier!
static void active_mod_queue_process_task(void *p)
{
	active_mod_packet active_packet;
	ESP_LOGI("Car", "Activate the Modifier");
	for(;;)
    {
		ESP_LOGI("Car", "Active modifier");
        if(xQueueReceive(active_mod_q, &active_packet, portMAX_DELAY) == pdTRUE)
        {
            // print_packet(recv_packet);
			printf("Received Active modifier: %02x\n", active_packet.modifier);
			if (active_packet.modifier == 1){
				start_time = millis()-1500;
				//current_time = start_time;
				printf("modifier: power down\n");
				brushed_motor_a(MCPWM_UNIT_0, MCPWM_TIMER_0, VSLOW);
				mod_flag = 1;
			}

			else if (active_packet.modifier == 2){
				start_time = millis();
				//current_time = start_time;
				printf("modifier: reverse control\n");
				rev = 1;
				mod_flag = 1;
			}
						
			else if (active_packet.modifier == 3){
				start_time = millis()-2000;
				//current_time = start_time;
				printf("modifier: stop control\n");
				brushed_motor_stop(MCPWM_UNIT_0, MCPWM_TIMER_0);
				mod_flag = 1;
			}
        }  
		else{
			taskYIELD();
		}   

    }
}


void recv_cb(const uint8_t * mac_addr, const uint8_t *data, int len) {

	//ESP_LOGI("Car", "%d bytes incoming from " MACSTR, len, MAC2STR(mac_addr));

	if(len == sizeof(controls_packet)){
		static controls_packet recv_packet;
		memcpy(&recv_packet, data, len);
		if (xQueueSend(ctrl_recv_q, &recv_packet, 0) != pdTRUE) {
			ESP_LOGW("Car", "Controls Queue full, discarded");
			return;
		}
	}
	else if (len == sizeof(modifier_packet)){
		static modifier_packet recv_packet;
		memcpy(&recv_packet, data, len);
		if (xQueueSend(tower_recv_q, &recv_packet, 0) != pdTRUE) {
			ESP_LOGW("Car", "Modifiers Queue full, discarded");
			return;
		}
	}
	else if (len == sizeof(active_mod_packet)){
		static active_mod_packet recv_packet;
		printf("recved activ mod: %02x\n", recv_packet.modifier);
		memcpy(&recv_packet, data, len);
		if (xQueueSend(active_mod_q, &recv_packet, 0) != pdTRUE) {
			ESP_LOGW("Car", "Modifiers Queue full, discarded");
			return;
		}
	}
	else{
		ESP_LOGE("Car", "Unrecognized packet size");
		return;
	}
}

void packet_sent_cb(const uint8_t* mac_addr, esp_now_send_status_t status){
	if(mac_addr==NULL){
		ESP_LOGE("Controller", "Send cb mac error");
		return;
	}
	printf(status==ESP_NOW_SEND_SUCCESS ? "ESP NOW Success\n" : status==ESP_NOW_SEND_FAIL ? "ESP NOW Fail\n" : "Unknown error occurred when sending packet\n");
}

//Initialize esp32 to enable send and receive
static void initialize_esp_now_car(void){
	// init NVS (storage) for wifi
	esp_err_t ret = nvs_flash_init();
	if(ret == ESP_ERR_NVS_NO_FREE_PAGES || ret == ESP_ERR_NVS_NEW_VERSION_FOUND){
		ESP_ERROR_CHECK(nvs_flash_erase());
		ret = nvs_flash_init();
	}
	ESP_ERROR_CHECK(ret);

	// init wifi
	ESP_ERROR_CHECK(esp_netif_init());
	ESP_ERROR_CHECK(esp_event_loop_create_default());  // check what this is for
	const wifi_init_config_t cfg = WIFI_INIT_CONFIG_DEFAULT();
	ESP_ERROR_CHECK(esp_wifi_init(&cfg));
	ESP_ERROR_CHECK(esp_wifi_set_storage(WIFI_STORAGE_RAM));
	ESP_ERROR_CHECK(esp_wifi_set_mode(WIFI_MODE_APSTA));  // set it to station and access point
	ESP_ERROR_CHECK(esp_wifi_start());

	// init ESP-NOW
	ESP_ERROR_CHECK(esp_now_init());
	ESP_ERROR_CHECK(esp_now_register_recv_cb(recv_cb));
	ESP_ERROR_CHECK(esp_now_register_send_cb(packet_sent_cb));
	ESP_ERROR_CHECK(esp_now_set_pmk((uint8_t*)CONFIG_ESPNOW_PMK)); // maybe dont need it since we're not encrypting packets

	// add tower as peer
	const esp_now_peer_info_t dest_peer1 = {
		.peer_addr = TOWER,
		.channel = 1,
		.ifidx = ESP_IF_WIFI_STA
	};
	
	const esp_now_peer_info_t dest_peer2 = {
		.peer_addr = ANOTHER_CAR, // another car
		.channel = 1,
		.ifidx = ESP_IF_WIFI_STA
	};

	const esp_now_peer_info_t dest_peer3 = {
		.peer_addr = CONTROLLER, // my controller
		.channel = 1,
		.ifidx = ESP_IF_WIFI_STA
	};

	ESP_ERROR_CHECK(esp_now_add_peer(&dest_peer1));
	ESP_ERROR_CHECK(esp_now_add_peer(&dest_peer2));
	ESP_ERROR_CHECK(esp_now_add_peer(&dest_peer3));
}

void tag_handler(uint8_t* serial_no){
	gpio_set_level(5, 1);
	for(int i = 0; i < 5; i++)
		printf("%#x ", serial_no[i]);

	printf("\n");
	gpio_set_level(5, 0);

	//time when car run over tag

	int64_t time_us = millis();

	tag_packet packet;// = malloc(sizeof(tag_packet));
	const uint8_t SRC_MAC[MAC_LEN] = MY_CAR;  // NOTE: must make it so we can choose car/ctrl 1 and 2
	memcpy(&(packet.src_mac), SRC_MAC, MAC_LEN);
	memcpy(&(packet.tag_id), serial_no, TAG_LEN); // read data from tag reader module

	printf("packet with soruce addr and tag id and time %lld\n", time_us);
	//memcpy(packet->lap_time, &time_us, sizeof(struct timeval));
	packet.lap_time = time_us;
	xQueueSend(tag_q, &packet, portMAX_DELAY);
}




void app_main(void) {
	mod_flag =0;
	const rc522_start_args_t start_args = {
		.miso_io = 16,
		.mosi_io = 4,
		.sck_io = 18,
		.sda_io = 15,
		.callback = &tag_handler
	};
	// ESP_ERROR_CHECK(rc522_start(start_args));
	rc522_start(start_args);

	const gpio_config_t pin_config1 = {
		.pin_bit_mask = ((1ULL << MOTOR_PIN_BW) | (1ULL << MOTOR_PIN_FW) | (1ULL << MOTOR_PIN_LEFT) | (1ULL << MOTOR_PIN_RIGHT)),
		.mode = GPIO_MODE_OUTPUT, //GPIO_MODE_INPUTOUTPUT, // for debugging output pins
		.intr_type = GPIO_INTR_DISABLE,
		.pull_down_en = 0,
		.pull_up_en = 0
	};
	ESP_ERROR_CHECK(gpio_config(&pin_config1));

	ctrl_recv_q = xQueueCreate(20, sizeof(controls_packet));

	tag_q = xQueueCreate(10, sizeof(tag_packet));
	tower_recv_q = xQueueCreate(10, sizeof(modifier_packet));
 	mod_q = xQueueCreate(10, sizeof(modifier_packet));
	active_mod_q = xQueueCreate(10, sizeof(active_mod_packet));

	initialize_esp_now_car();
	mcpwm_example_gpio_initialize();

	xTaskCreate(ctrl_queue_process_task, "Receive_from_controller", 2048, NULL, 2, NULL);
	xTaskCreate(tag_queue_send_task, "Send_info_to_Tower", 2048, NULL, 3, NULL);
	xTaskCreate(tower_queue_process_task, "Receive_from_tower", 2048, NULL, 5, NULL);
	xTaskCreate(active_mod_queue_process_task, "Receive active modifier", 2048, NULL, 5, NULL);
	//xTaskCreate(test_comm_task, "Send_info_to_Tower", 2048, NULL, 2, NULL);
	//xTaskCreate(mcpwm_example_config, "mcpwm_example_config", 4096, NULL, 5, NULL);
	// xTaskCreate(print_outputs, "Print_GPIO_outputs", 2048, NULL, 1, NULL);
	//xTaskCreate(activate_mod, "activate_mod", 2048, NULL, 5, NULL);
}

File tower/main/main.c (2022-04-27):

#include <stdio.h>
#include <string.h>
#include <stdlib.h>
#include <sys/time.h>
#include "freertos/FreeRTOS.h"
#include "freertos/task.h"
#include "freertos/event_groups.h"
#include "freertos/queue.h"
#include "driver/gpio.h"
#include "nvs_flash.h"
#include "esp_netif.h"
#include "esp_wifi.h"
#include "esp_log.h"
#include "esp_now.h"
#include "esp_system.h"
#include "esp_sleep.h"
#include "strmap.h"

#include "../../config/mario_kart_config.h"
#include "display.h"

#define NCHECKPOINTS 5

static xQueueHandle recv_q;
static xQueueHandle modifier_q;

bool start_game;
//hash map Definition for tag information
StrMap *sm; 	 // address of the start point of the string map
char value[4]; // buffer to copy the value of a certain key
int current_time;
int start_time;

// Car_Status Car1_status = { .checkpoint = 0, .lap_min = 0, .lap_sec = 0, .lap_ms = 0, .curr_lap = 0 };
// Car_Status Car2_status = { .checkpoint = 0, .lap_min = 0, .lap_sec = 0, .lap_ms = 0, .curr_lap = 0 };
// const uint8_t car1_mac[MAC_LEN] = CAR1_MAC_ADDR;
// const uint8_t car2_mac[MAC_LEN] = CAR2_MAC_ADDR;

Start_pack Start_information = { .car1_start_time = 0,.car2_start_time=0, .user_num = 0, .lap_num = 0 };

Race race;

int64_t millis() {
	struct timeval tv;
	gettimeofday(&tv, NULL);
	return (tv.tv_sec * 1000LL + (tv.tv_usec / 1000LL));
}


// void set_start_time(int8_t user, int8_t lap){
// 	start_time = millis();
// 	Start_information.start_time = start_time;
//     Start_information.lap_num = lap;
// 	Start_information.user_num = user;
// }

void reset_race_stat(int8_t user){
	// free(race.car1_times);
	// if(user > 1){
	// 	free(race.car2_times);
	// }
	start_game = false;
	printf("[Race Stoped] Reset Races Statistics\n");
}

// call this function whenever the user clicks the "start" button on screen
// initializes the race struct which contains information on lap
void start_race(int8_t user, int8_t lap){
	int i;
	int time_array_size = NCHECKPOINTS * Start_information.lap_num + 1;
	start_time = millis();
	Start_information.car1_start_time = -1;
	Start_information.car2_start_time = -1;
    Start_information.lap_num = lap;
	Start_information.user_num = user;

	race.car1.checkpoint = 0;
	race.car1.curr_lap = 0;
	for (i = 0; i < time_array_size; ++i)
    	race.car1_times[i] = 0;
	race.car1.lap_min = 0;
	race.car1.lap_sec = 0;
	race.car1.lap_ms = 0;
	race.car1.race_end = false;
	race.car1.win = false;
	race.car1.modifier = 5;

	if(user > 1){
		race.car2.checkpoint = 0;
		race.car2.curr_lap = 0;
		for (i = 0; i < time_array_size; ++i)
    		race.car2_times[i] = 0;	
		race.car2.lap_min = 0;
		race.car2.lap_sec = 0;
		race.car2.lap_ms = 0;
		race.car2.race_end = false;
		race.car2.win = false;
		race.car2.modifier = 5;
	}
	start_game = true;
	printf("start information updated\n");
}

uint8_t random_modifier(){
	//return values: 
	//	0: power up
	//	1: power down
	//	2: reverse control
	//	3: stop
	//return (uint8_t) (esp_random() % 4);
	return 0;
}

void update_checkpoint(uint8_t car_id, uint8_t checkpoint, uint64_t time){
	printf("checkpoint tagged: %d\n", checkpoint);
	Car_Status* this_car;
	Car_Status* other_car;
	uint64_t * time_array;
	uint64_t* car_start_time;
	if (car_id == 1){
		printf("Car 1: \n	Checkpoint Update\n");
		this_car = &race.car1;
		other_car = &race.car2;
		time_array = race.car1_times;
		car_start_time = &Start_information.car1_start_time;
	}
	else if (car_id == 2){
		printf("Car 2: \n	Checkpoint Update\n");
		this_car = &race.car2;
		other_car = &race.car1;
		time_array = race.car2_times;
		car_start_time = &Start_information.car2_start_time;
	}
	else {
		return;
	}

	// When Passing the Start Line
	if (*car_start_time == -1){
		if (checkpoint == 0){
			printf("	Start Line passed!/n");
			*car_start_time = time;
			time_array[0] = 0;
			this_car->curr_lap += 1;
		}
		else{
			printf("	You did not passed the start line!\n");
			return;
		}
	}
	else if (this_car->race_end) { // When Player passed the Finish Line
		printf("[USER 1]RACE ALREADY ENDED\n");
		return;
	}
	else{ // When Player is in between the race
		if (((this_car->checkpoint + 1) % NCHECKPOINTS) == checkpoint){
			printf("	Correct checkpoint passed \n");
			uint64_t lap_time;
			uint8_t lap = this_car->curr_lap;
			this_car->checkpoint = checkpoint;

			if (checkpoint == 0){ // when starting new lap
				printf("		Checkpoint is 0\n		NEW LAP!\n");
				lap_time = time - *car_start_time - time_array[NCHECKPOINTS*(lap-1)];
				this_car->curr_lap += 1;
				lap += 1;
				time_array[checkpoint + NCHECKPOINTS * (lap-1)] = time - *car_start_time;
			}
			else{
				printf("		Checkpoint is %d\n", checkpoint);
				time_array[checkpoint + NCHECKPOINTS * (lap-1)] = time - *car_start_time;
				lap_time = time - *car_start_time - time_array[NCHECKPOINTS*(lap-1)];
			}


			if (lap > Start_information.lap_num){ // when race ends
				printf("	End Line Passed! \n");
				this_car->race_end = true;
				this_car->curr_lap = Start_information.lap_num;
				if (Start_information.user_num == 1){
					this_car->win = true;
					race.winner = true;
				}
				else if (!(other_car->win)){
						this_car->win = true;
				}
				else{
					if (race.car1_times[5*Start_information.lap_num] > race.car2_times[5*Start_information.lap_num]){
						race.winner = true;
					}
				}
				lap_time = time - *car_start_time;
			}
			else{
				printf("time array lap start time : %lld\n", time_array[NCHECKPOINTS*(lap-1)]);
			}
			this_car->lap_min = lap_time/60000;
			this_car->lap_sec = (lap_time%60000)/1000;
			this_car->lap_ms = lap_time%61000;
		}
	}
}
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

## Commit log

2022-01-31 failing to transmit data
    [main.c]
2022-02-04 added new esp32s
2022-02-11 adding pwm.c module
2022-02-13 controller schematics
    [car circuit.kicad_pcb, controller.sch]
2022-02-16 update PWM
2022-02-16 Car schematics
    schematics for the car with the motor control L298
    [motor control.kicad_pcb, motor control.kicad_sch, motor control.sch]
2022-02-18 updated controller schematic
    [controller.sch]
2022-02-19 update all power for 1 car
2022-02-23 added drivers for display
    [controller.kicad_pcb, controller.sch]
2022-02-28 tower pcb
    [controller.kicad_pcb, tower.kicad_pcb, tower.sch]
2022-02-28 Car schematics
    car schematics almost finished
    [car (1).kicad_pcb, car (1).kicad_sch, car (1).sch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]
2022-03-03 finished (I think) schematics for tower and controller
    [controller.kicad_pcb, controller.sch, tower.kicad_pcb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]
2022-03-03 car presentation
    is done for now...
    [car (1).kicad_pcb, car (1).kicad_sch, car (1).sch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]
2022-03-03 car updated hopefully works
    temp file to see if error
    [car_updated.kicad_pcb]
2022-03-03 new folder
    new folder
    [car (1).kicad_pcb, car (1).kicad_sch, car (1).sch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]
2022-03-03 converted all schematics into kicad6 format
    [car (1).kicad_pcb, car (1).kicad_sch, car (1).sch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]
2022-03-09 think Ive finished the schematics
    [car.kicad_pcb, controller.kicad_pcb, controller.kicad_sch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]
2022-03-10 final pcbs and schematics
    [car (1)-B_Cu.gbr, car (1)-B_Mask.gbr, car (1)-B_Paste.gbr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]
2022-03-30 updated pins for controller
    [car.csv, controller.csv, tower.csv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]
